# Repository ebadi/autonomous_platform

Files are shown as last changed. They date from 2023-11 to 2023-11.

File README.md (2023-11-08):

# Autonomous Platform (Gen4)

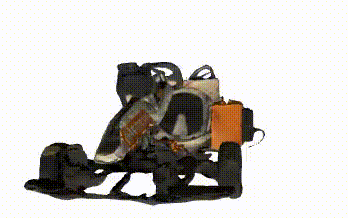
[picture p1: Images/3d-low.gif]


This is the repository for Autonomous Platform at Infotiv Technology Development. The new generation of Autonomous Platform was created by **Fredrik Juthe** and **Erik Magnusson** as part of a master thesis at Chalmers University of technology spring 2023 under supervision of **Hamid Ebadi**. The master thesis designed the system E/E architecture and implemented a base on which future functionality could be added to. A published version of the thesis with the title of **"Design of a modular centralized E/E and software architecture for a small-scale automotive platform"** is accessible in [in this link PDF ](Master_Thesis2023.pdf).

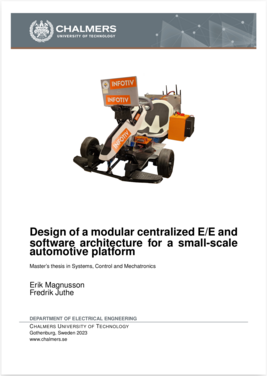
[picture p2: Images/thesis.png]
Design of a modular centralized E/E and software architecture for a small-scale automotive platform


INFOTIV logo (https://www.infotiv.se)
Chalmers logo (https://www.chalmers.se)

- The __latest public__ version of documentation and source code for Autonomous Platform (AP) project is available in the following address: [https://infotiv-research.github.io](https://infotiv-research.github.io) and [https://github.com/infotiv-research](https://github.com/infotiv-research).
- The printer friendly version of this document is [available in this link PDF](AutonomousPlatform.pdf).

## Introduction

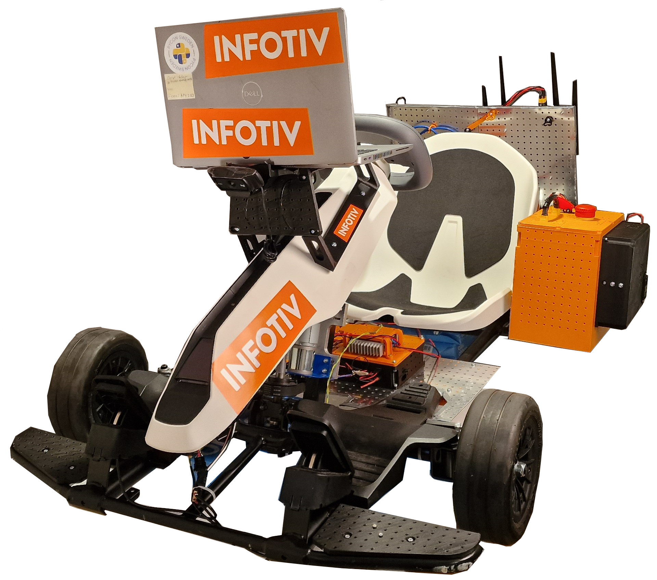
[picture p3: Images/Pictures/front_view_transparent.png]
Front view of platform after Master's thesis spring 2023


Autonomous Platform (generation 4) project is a platform on which internal and external research projects can be tested on. (i.e Autonomous Drive algorithms) and to expand the knowledgeable in different aspects of software and hardware system development. The purpose of this repository is to collect all the software components in one mono-repository, meaning all software (& hardware design) for the different components is placed in a single repository. Any future work on autonomous platform should be integrated into one of the repositories sub directories. This means that any future development or research can always refer back to previous work, making it a viable long term project at Infotiv AB.

## Features and Capabilities 

Below, the capabilities and functions of autonomous platform generation 4 are summarized.

### Drive by wireless controller

AP4 is capable to be remotely controlled using an xbox 360 controller.  The xbox wireless adapter should be connected to the Raspberry Pi 4b usb port.

### Remote access to platform & software

A wifi router is mounted on the back plate, this allows developers to connect to the software whilst it is running to monitor internal states. High-level software can stream commands to the low-level software remotely.

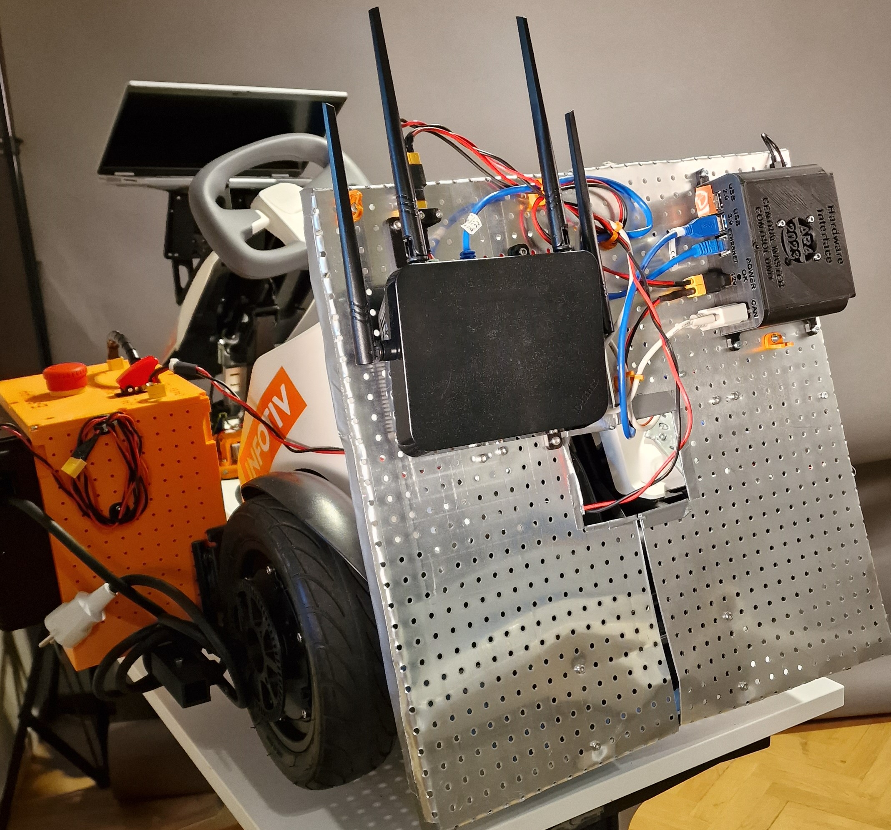
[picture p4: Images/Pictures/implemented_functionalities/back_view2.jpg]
View of the backplate where the wifi router and Raspberry Pi is mounted


### Accelerating, Brake & Steering

The platform can be driven forwards, backwards and can be steered. This is done programmatically, meaning "Drive by Wire". Joysticks commands from the xbox controller can therefore be configured to control the platform. In the same way it is trivial to take commands from Autonomous Drive algorithms to control the platform.

### Scalability

The idea with autonomous platform generation 4 is that it should be a scalable base platform on with future functionality should be added onto. Scalability and modularity is therefore a key concept for the platform. 

Hardware wise, every component can be mounted where it is deemed appropriate using a pre defined hole pattern. It is possible to move existing hardware as time goes on. New hardware can be added as long as it uses the pre defined hole pattern present on the metal sheets.

Embedded sensors can be added using ECUs following a set template. These can then be added to the existing system without breaking backwards compatibility using a defined CAN bus network. High data throughput sensors can be added to the platform using USB connection.

The software is built to be scalable and modular. The software structure is described in detail below. The software is deployed inside docker containers, making it easily deployable and scalable. The controlling software is written using the Robot Operating System 2 (ROS2) Framework. This allows developers to easily add onto existing software.

### Power Module

Consists of a led acid battery and a power supply unit, both can be connected to power the autonomous platform. Meaning the platform can be powered whilst driving around from battery. Whilst in a lab environment power can be supplied to the platform through a wall socket.

### Digital Twin 

The digital twin is implemented in the high-level software. It is described in detail in `High_Level_Control_Computer/README.md`. It is automatically started when the high-level docker container is started.

## System Architecture 

The autonomous platform has three different software components:

- High-level control
- Low-level control
- Embedded control

High-level is supposed to be run on a high performance computer and can be run without being connected to the rest of the system. Low-level control is run on the Raspberry Pi 4b mounted on the hardware platform. The embedded control is run on the ECU nodes mounted to the platform. Software in high-level and low-level are communicating using the Robot Operating System (ROS2) framework. Software in the embedded control is written using the Arduino framework.

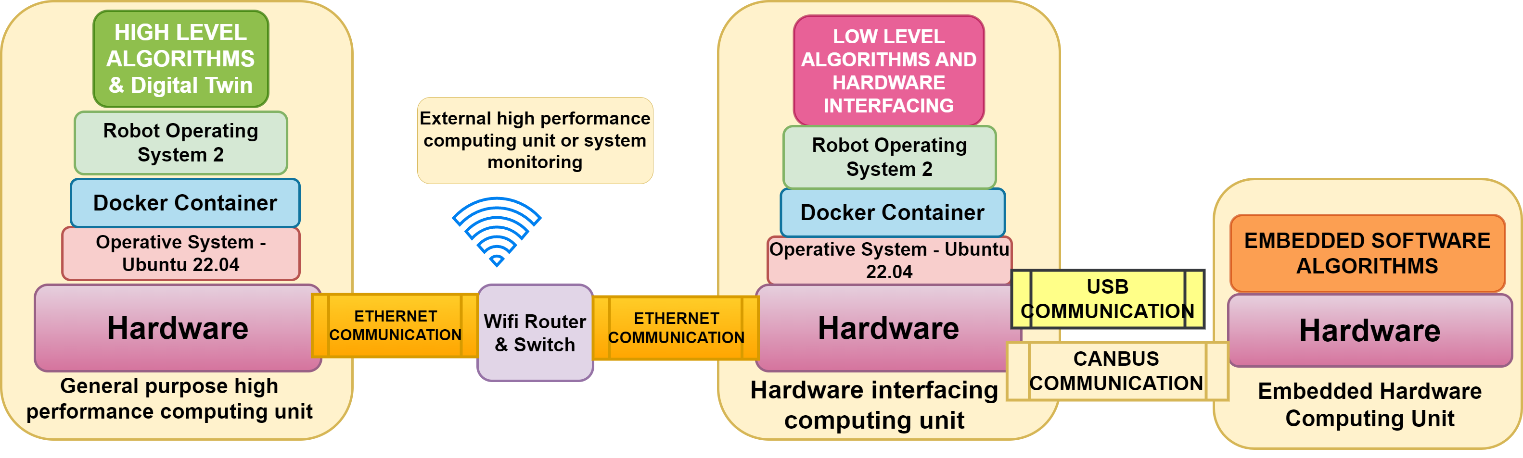
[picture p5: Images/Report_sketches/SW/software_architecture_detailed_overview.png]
System architecture and software layers illustrated
 

The three software components are connected through hardware and software links. High-level and low-level software is connected using an ethernet interface, meaning the two softwares should be run whilst connected to the same network. The low-level control is connected to the embedded control through a CAN bus network. A custom CAN library and interface has been created to link the embedded control with the low-level control.

###  High-level control

The high-level software consists of three components, an autonomous driving algorithm and a digital twin interface with the Gazebo physics simulator and a switch which sends commands to either the digital twin or the physical platform. As of June 2023 only a simple digital twin is implemented in this software layer. Starting up the high-level control container will start up Gazebo and Rviz. See `FUTURE_WORK.md` for what could be implemented.

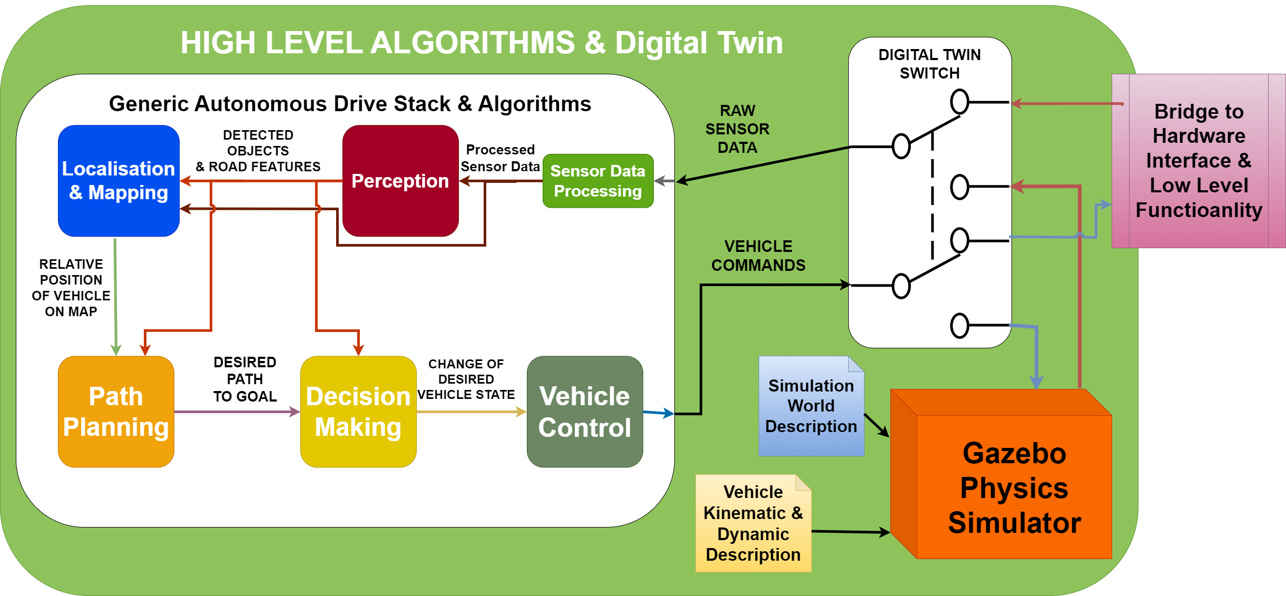
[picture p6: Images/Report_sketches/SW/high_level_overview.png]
high level overview
 
In the illustration above, three components can be seen. Autonomous driving stack, digital switch and gazebo physics simulator. These components should be implemented as a set of ROS2 computational nodes. Note: This is the intended structure but has not been implemented yet.

* __Autonomous Drving Stack__ is the proposed set of algorithms which takes in sensor information and responds with suitable actuator control commands. 
* __Digital Twin Switch__ is the proposed software switch that is supposed to re-route AD commands to either the physical platform or the digital twin. In the same way, sensory data should be routed from the physical platform or digital twin. The same actuator commands and sensor data type should be used on the digital twin as the physical platform. This ensures that proposed AD algorithms can first be tested on the digital twin and then seamlessly be tested on the physical platform.
* __Gazebo Physics Simulator__ Is the proposed digital twin simulation environment. It integrates seamlessly with the ROS2 framework. The physical dimensions and driving dynamics can be configured in xml format. Different simulation environments can be setup and saved as world files. Meaning different AD scenarios can be tested easily.

The high level control folder, `High_Level_Control_Computer` consist of a docker container and a folder with software. The software can start a simple digital twin of Autonomous platform Generation 4. The folder contains a `docker-compose` file which starts a docker container and mounts the `ap4_hlc_code` folder in the container. A ROS2 launch file is then run which starts up the digital twin. The container can be started on any device supporting graphics, i.e a laptop. 

###  Low-level control

The low-level software is responsible for taking platform commands sent from higher-level software and convert it into commands which are sent to the actuators. It is implemented on a Raspberry Pi 4b. A simple vehicle control converts commands sent on `\cmd_vel` ROS2 topic into ROS2 topics which gets relayed to the embedded control. In the same way the low-level software is responsible for taking any sensor input and passing it forwards to higher-level software. A custom package to convert ROS2 topics into CAN bus has been created, making it simple to interface high-level software with the embedded control software.

The hardware interface folder, `Hardware_Interface_Low_level_pc` , contains a `docker-compose` file which starts a docker container and mounts the `ap4_hwi_code` folder in the container. A ROS2 launch file is then run which starts up software that interfaces with hardware. This software is specific for the hardware mounted on autonomous platform, therefore it can only be started properly on the Raspberry Pi 4b mounted onto the platform.

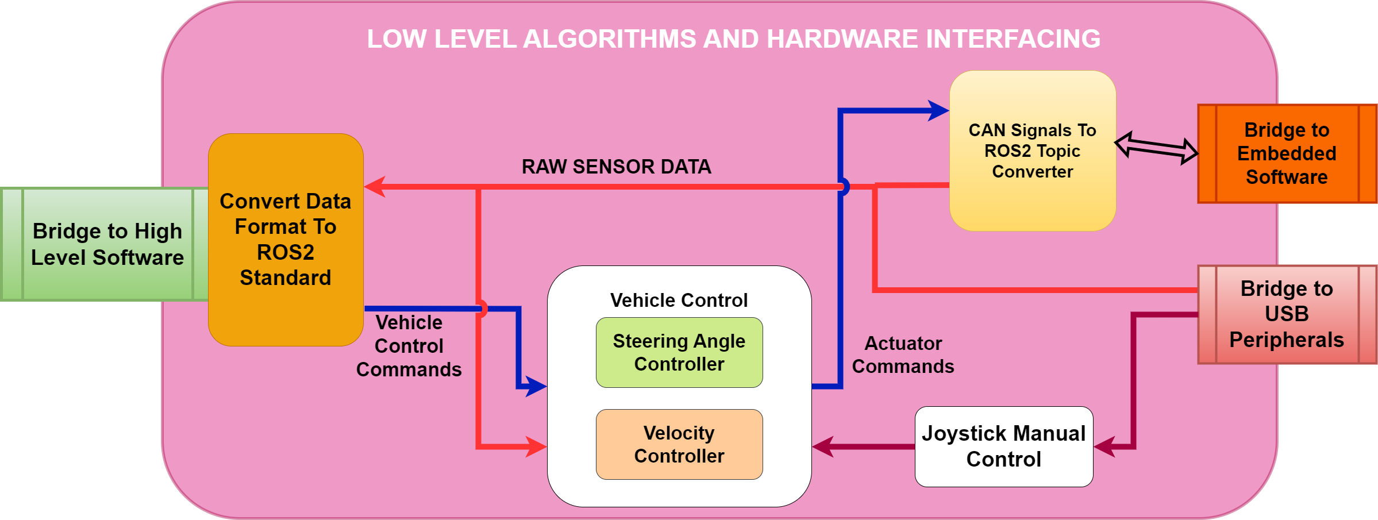
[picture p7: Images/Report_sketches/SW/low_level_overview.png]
low level overview
 

### Embedded control

The embedded software is implemented on the ECUs placed on the platform. This firmware acts as an interface between hardware (actuators or sensors) and pass data to and from the low-level software.
Currently a single embedded software is implemented, Steering and Propulsion Control Unit (SPCU).

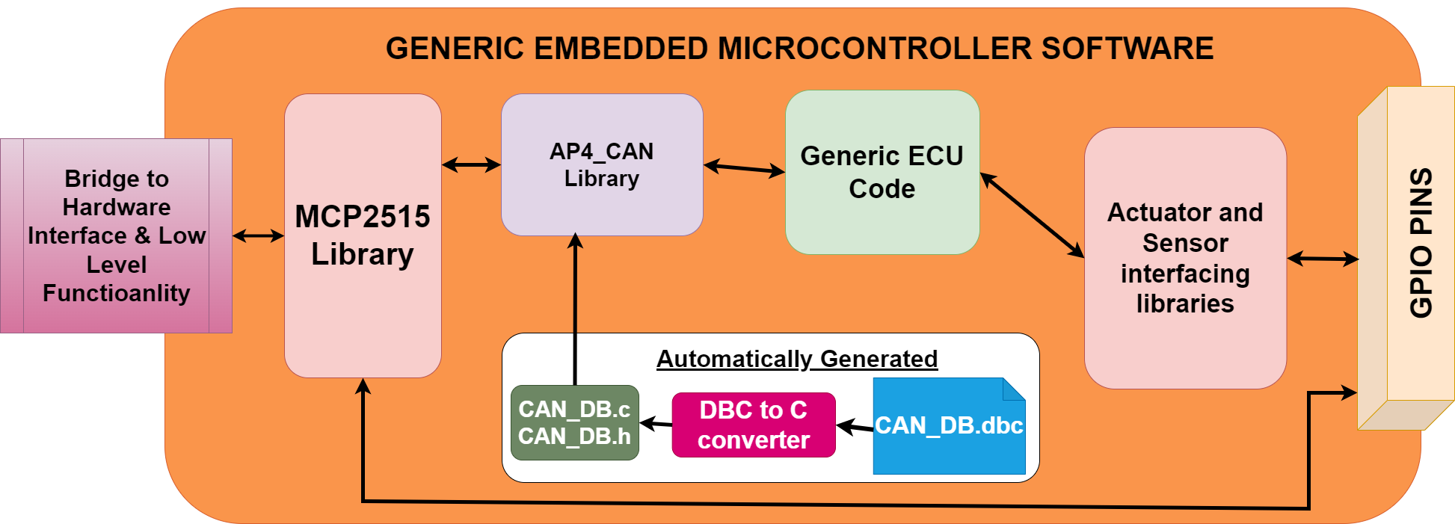
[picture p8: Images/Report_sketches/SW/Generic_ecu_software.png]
Embedded control
 

`CAN_Nodes_Microcontroller_Code` folder contain PlatformIO projects for each ECU, that is the embedded software running on the generic ECUs. An example of ECU is the SPCU (Steering, Propulsion Control Unit).Furthermore here is the CAN database and the corresponding CAN-library located.

## Start AP4 

Below follows a quick guide on how to start autonomous platform generation 4 and control it using an xbox 360 controller.

* Connect xbox wireless adapter to Raspberry Pi 4b
* Connect Power source: (Battery or PSU) to POWER IN plug. 
* Release Emergency stop
* Flip start switch
* Turn on Nine-bot segway (on backside of platform) Segway will beep once.

System will now boot up. The wheels will move back and forth.

* Wait 60 seconds (hardcoded in the SPCU ECU unit)

The platform should beep again after waiting 60 seconds and turn right to left, meaning it is ready to use.

The platform should be controllable using the xbox controller. By holding down the X button and moving the left joystick the front wheels should move and back wheels turn forwards.

## Connect (wireless) and start AP software stack

To check that the software is up and running as expected one can connect to the platform wirelessly and monitor the ROS2 network. On an external computer (dev-laptop or other linux computer) start the high-level software container. Make sure the computer is connected to the wifi network of autonomous platform. 

NOTE: User credentials are available only in the infotiv internal gitlab repository.

NOTE: high-level software automatically starts the digital twin simulation environment, the RVIZ and gazebo windows can be ignored.

In a new terminal, start the docker container:

```bash
cd High_Level_Control_Computer
docker-compose build
docker-compose up
```

In a new terminal, enter the docker container
```bash
docker exec -it ap4hlc bash
```

Source environment variables and export configuration environment variables
```bash
cd ap4hlc_ws
source install/setup.bash
export ROS_DOMAIN_ID=1
```

The low-level software components should be visible to the high level software components. This can be checked with
```bash
ros2 node list
```
The expected output will be something like this:

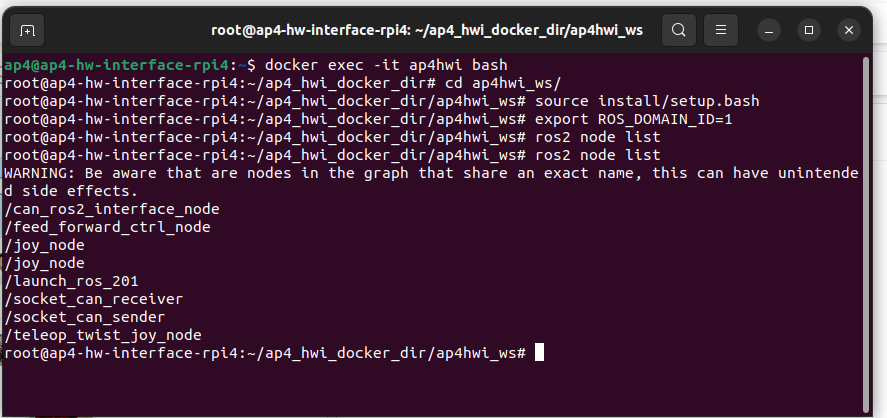
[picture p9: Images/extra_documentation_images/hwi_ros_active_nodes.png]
ROS active nodes


Information sent between nodes (such as sensor data or CAN bus traffic) can be monitored using
```bash
ros2 topic echo <topic_name>
```

For a list of active ROS2 topics, the following command can be used.

```bash
ros2 topic list
```

If the topics and nodes show up, the system has started correctly and can be controlled by either an xbox control or any future high-level software control. 

## Repository overview
The repository consists of three directories containing software (with a few subdirectories each):

 * [`CAN_Nodes_Microcontroller_Code`](CAN_Nodes_Microcontroller_Code/)
 * [`Hardware_Interface_Low_Level_Computer`](Hardware_Interface_Low_Level_Computer/) 
 * [`High_Level_Control_Computer`](High_Level_Control_Computer/) 

Within these directories, there exists useful documentation regarding each software component and sub components.

* `CAN_Nodes_Microcontroller_Code/README.md`
* `CAN_Nodes_Microcontroller_Code/CAN_LIBRARY_DATABASE/README.md`
* `Hardware_Interface_Low_Level_Computer/README.md` 
* `High_Level_Control_Computer/README.md`

The documentation is split up into smaller parts to keep information manageable and separated according to what can be relevant at a given time. The major documentation files located in the root directory of the repository are:

* [`README.md`](README.md) : The documentation you first see when you open the gitlab, this document. 
* [`SOFTWARE_DESIGN.md`](SOFTWARE_DESIGN.md) : A quick introduction to important software and frameworks used on AP4 and how to install the required software. In illustration of how the network of hardware is connected is also can be found there.
* [`HARDWARE_DESIGN.md`](HARDWARE_DESIGN.md) : An introduction to hardware that is used on AP4 and how to add a new one.
* [`HOW_TO_EXTEND.md`](HOW_TO_EXTEND.md) : Are you a new team member? Look at this file for a quick introduction to the project and how to get going. It also has a general design principles for the project to keep in mind when adding new functionality.
* [`TEST_DEBUGGING.md`](TEST_DEBUGGING.md) : Contains a list of known errors when working with AP4 and how to solve them
* [`ISSUES_AND_FUTURE_WORK.md`](ISSUES_AND_FUTURE_WORK.md) : A Comprehensive list of known bugs & issues and possible future work to be done on the platform.
* [`REQ_SPEC_BOOM.xlsx`](REQ_SPEC_BOOM.xlsx) contains a list of decided upon requirements and specifications which the autonomous platform should follow. A complete bill of materials (hardware components) can be found in this file. It contains items, what purpose they serve, where they can be bought and a total estimated cost.
As of *June 2023* the total cost is 16500 SEK to build the base platform and have spare parts over.

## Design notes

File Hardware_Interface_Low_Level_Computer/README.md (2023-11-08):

# Low-level Control & Hardware

## Introduction
This directory contains the software stack running on the Raspberry Pi 4b mounted to the hardware platform. It also aims to describe how each software component is designed / implemented.

In summary, the Low-level Control & Hardware Interface SW & HW is Hardware specific. It shall be run on the platform, connected to the embedded SW, CAN busses etc. It works as a bridge between high-level control software and the embedded ECU code which controls actuators / reads sensor data. 

Below an illustration of the low level and hardware interfacing software can be seen.

Low level overview

The software itself is implemented using the ROS2 framework, this software is then run inside a docker container. It is only meant to run on the Raspberry Pi 4b mounted onto autonomous platform and is very hardware specific. 

In the diagram above, four ROS2 packages are illustrated as rounded rectangles. These are;

## CAN Signals To ROS2 Topic Converter
This is a custom made ROS2 package made spring 2023. The purpose of it is to be a software translation of the CAN bus data from the embedded software layer to useful information available on ROS2 topics.

This abstracts the transfer of information between low level software and embedded software running on ECUs in the CAN network.

It uses the unified CAN bus database file (.dbc) for autonomous platform in order to decode the information sent on the CAN network. This database file is located at `autonomous_platform\CAN_Nodes_Microcontroller_Code\CAN_LIBRARY_DATABASE\CAN_DB.dbc`. A custom application is then written that maps a specific CAN signal onto a specific ROS2 topic. This means that every data signal sent over the CAN network can be used in algorithms located in the hardware interface and low level software. In the same way, ROS2 topics can be used to set the value of certain signals, meaning commands can be sent from the hardware interface and low level software to the various ECUs mounted onto autonomous platform.

### Vehicle Control
This is a custom made ROS2 package to control the steering angle and velocity of the hardware on a low level. It receives a desired velocity and steering angle on the `/cmd_vel` ROS2 topic and uses a controller gain to scale the values. The values have to be processed and rescaled in order for the embedded ECUs to actuate correctly. 

I.e to control the velocity, the embedded software in the SPCU expects a desired voltage to be sent on the CAN bus. Therefore the desired velocity needs to be converted into a desired voltage that should be applied on the accelerator pedal.

**More advanced control behavior can be implemented later on, I.e some sort of feedback from the velocity sensors. As of now it is open loop controlled**

### Joystick Manual Control
This is a set of ROS2 packages which enables a joystick to be connected to autonomous platform. The output will be in the form of a velocity commands on the `/cmd_vel` ROS2 topic. This output can then be read in vehicle control to control the gokart.

### Convert Data Format To ROS2 Standard
**This is not implemented yet for every data input**

The software layer connected to the hardware interfacing software layer expects input and output to be on specific ROS2 topics and uses standard ROS2 interfaces. I.e velocity commands to the platform will come to the hardware interfacing and low level software on the topic `/cmd_vel`, it is then up to this ROS2 package to convert it to a format which the lower level algorithms can use.

This can be as an abstraction layer.

The rectangular squares in the diagram above can be seen as input and outputs to the hardware interface and low level software layer. Higher level commands to the platform will come from the high level software. In the same way, this software layer will interface with the CAN network and USB peripherals for input and output. 

### Low-Level Control & Hardware Interface - Software / Hardware Requirements 

In terms of hardware, the low-level control software and hardware interfacing software is run on a Raspberry Pi 4b 4Gb. A RS485 CAN hat has been installed onto the GPIO pins. Power (5V,3A) is supplied from the platform using an LM2596 DC-DC converter to step down the platforms 12V power supply to 5V. A 32GB micro SD card is all the storage available. The hardware should be connected to the CAN network on Autonomous Platform Generation 4 (DB9 Connector) and to the wifi router/switch through an ethernet cable.

* [Raspberry Pi 4b Specifications](https://www.raspberrypi.com/products/raspberry-pi-4-model-b/specifications/)
* [RS485 CAN HAT Specifications](https://www.waveshare.com/w/upload/2/29/RS485-CAN-HAT-user-manuakl-en.pdf)
* [LM2596 Specifications](https://www.ti.com/lit/ds/symlink/lm2596.pdf)

Software wise, it uses a base installation of Ubuntu 22.04. A detailed guide on how to setup the software on a new fresh Raspberry Pi 4b can be found [here](#Installing-Base-Software-on-Fresh-Raspberry-Pi-4b).

When developing code for the low-level software it is possible to open the low-level software docker container on any linux based computer. It can be useful to have access to a proper IDE and not have to write code in notepad. Note: the CAN bus interfacing libraries will throw errors due to not being connected hardware wise. But once software compiles changes can be pushed and then pulled to the raspberry pi 4b.

### USB Devices Connected
There exists a USB hub mounted to the autonomous platform. This is connected to the Raspberry Pi 4b.

The following devices are connected
* Wireless keyboard and mouse
* Xbox Wireless Adapter

**Currently the USB hub is not mounted**

### Interfacing With Embedded ECUs 
The hardware interface and low level software can communicate with the embedded ECUs. Physically this is done through a Controller Area Network (CAN) bus with a D-Sub 9 connector. Software wise, a custom solution has been implemented for autonomous platform. The data sent over the CAN bus needs to be available on ROS2 topics in order for ROS2 nodes to be able to use the data in computations. In the same way, actuator commands sent from ROS2 nodes on ROS2 topics need to be sent to the ECUs over CAN.

The CAN frames sent over the CAN network must be encoded and decoded correctly and in the same way on both the hardware interface and embedded ECUs. Therefore a unified CAN database file has been constructed for autonomous platform . A helper library is used to convert the CAN database file into a set of C-style data structures.

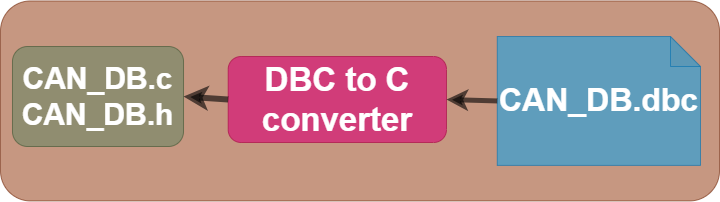
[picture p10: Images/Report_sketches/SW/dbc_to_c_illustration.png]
CAN communication information transportation illustration.
 

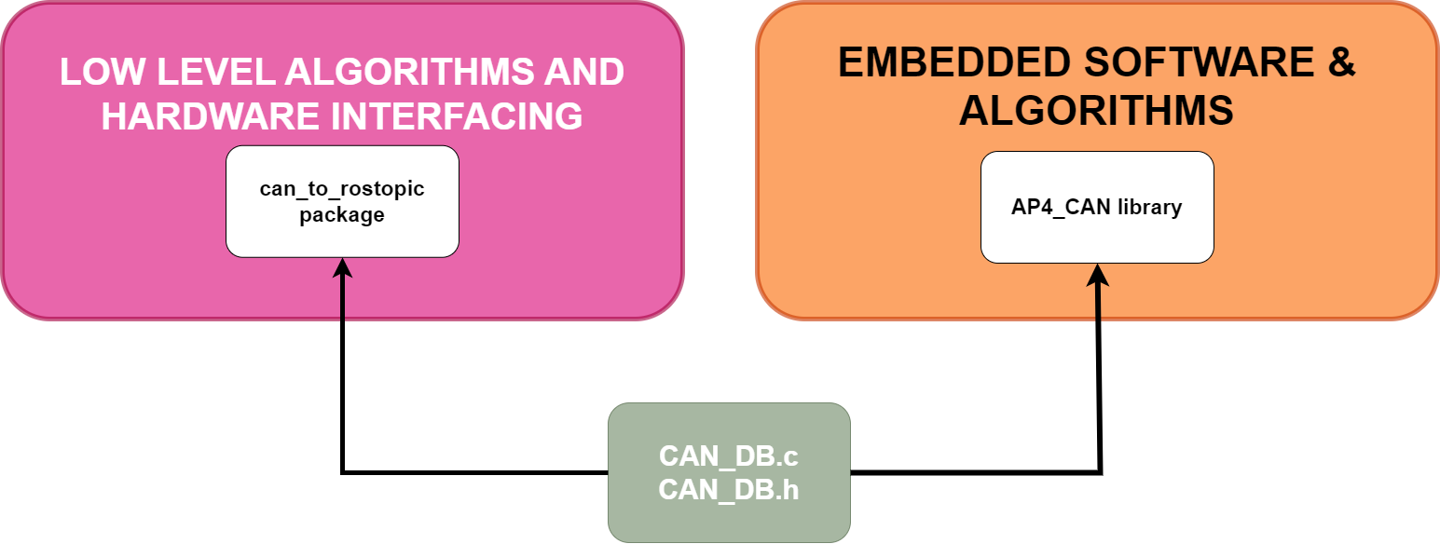
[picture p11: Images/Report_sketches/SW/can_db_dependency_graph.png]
 

Two custom made libraries have then been implemented, one in the embedded software and one in ROS2 in hardware interface and low level software.

How to extend this functionality with new CAN frames and signals is explained in detail in `Hardware_Interface_Low_Level_Computer\HOW_TO_EXTEND.md`. (The parts that are relevant to change in hardware interface and low level software is documented here). How to extended the software for the embedded ECUs is described in `CAN_Nodes_Microcontroller_Code\HOW_TO_EXTEND.md`.

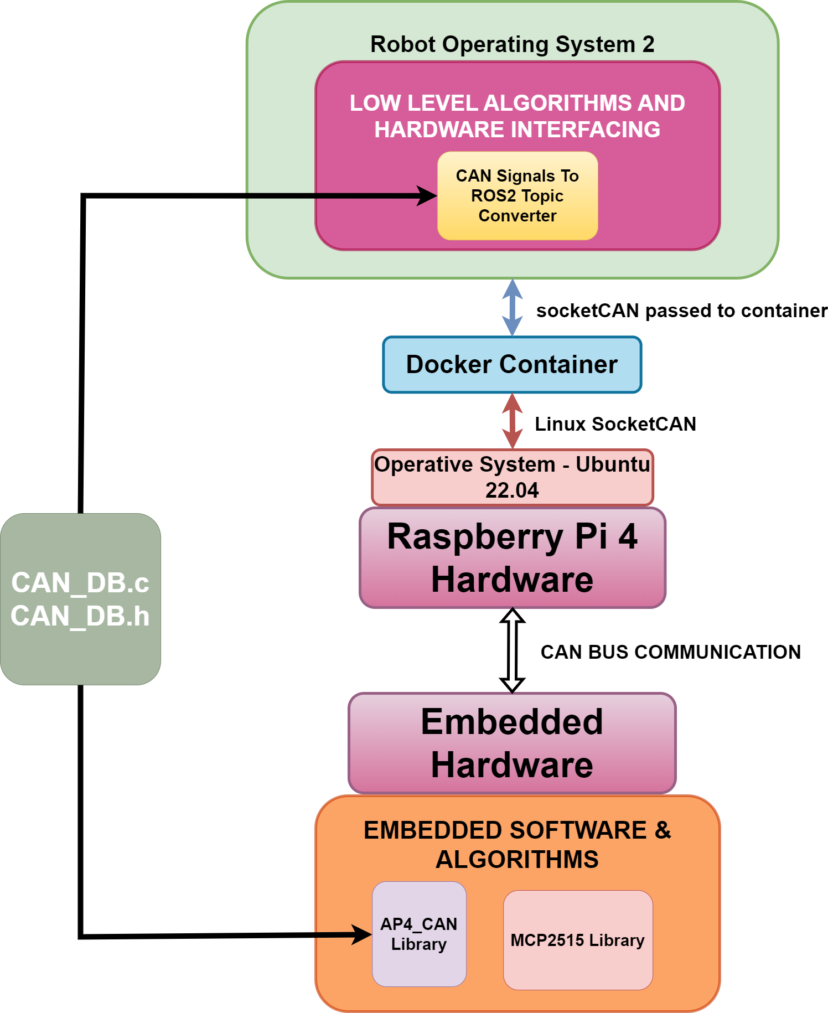
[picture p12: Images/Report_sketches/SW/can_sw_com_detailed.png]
 

### Interfacing with High Level Control Software 
The hardware interface and low level software can communicate with the high level control software running on an external computer. (I.e linux laptop- or intel NUC) This is done through an ethernet communication. A Wifi router is mounted to autonomous platform which means this can be done wirelessly.

Once an ethernet connection has been established, the two distinct ROS2 software networks (one on raspberry pi and one one on laptop) will be able to detect each other. This means that the two smaller ROS2 networks of nodes will become one large network with distributed computing power.

Network SSID and password is noted down in main `README.md` file of repository.

An important note, the ROS_DOMAIN_ID has to be configured to the value of 1 on both ROS2 networks.

### Adding New Functionalities 

How to add new functionality to the hardware interfacing software and low level algorithms is explained in `Hardware_Interface_Low_Level_Computer\HOW_TO_EXTEND.md`. 

### Automatic Startup of Software 
Once the Raspberry Pi 4b boots up it will automatically start the hardware interfacing and low level algorithm software. This is done using linux services that run on boot-up which in turn call the script "testing.bash".

If you need to change what is done during boot-up, edit the `testing.bash` script.

If the software does not automatically start, see **Software container not started?** in  `TEST_DEBUGGING.md` located in this directory.

### Installing Base Software on Fresh Raspberry Pi 4b 
See section in `SETUP_OF_RASPBERRY_PI.md`

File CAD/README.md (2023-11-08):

# CAD Appendix

<!---  AUTOMATICALLY GENERATED FILE. DONT EDIT THIS FILE DIRECTLY. EDIT thumbnail.sh INSTEAD --> 
STL files can be opened using any 3D printer slicer software, at Infotiv we use 'Ideamaker'. [Download here](https://www.raise3d.com/ideamaker/). Use a slicer configuration for an 'Raise3d E2' 3d printer. PLA material choice is fine if you don't leave autonomous platform in a hot car during the day. A base slicer profile for the Raise3D E2 can be found in the CAD profile. It is a nice starting point.

./Limitswitch_steering_holder/limittswitch_bottom_holder.stl:

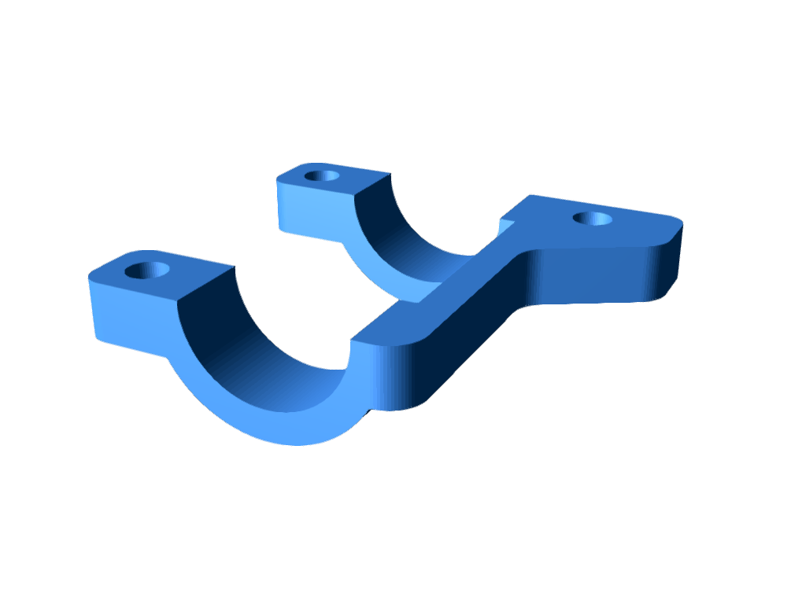
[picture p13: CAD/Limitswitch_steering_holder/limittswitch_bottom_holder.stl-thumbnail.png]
./Limitswitch_steering_holder/limittswitch_bottom_holder.stl


./Limitswitch_steering_holder/limitswitch_holder_top.stl:

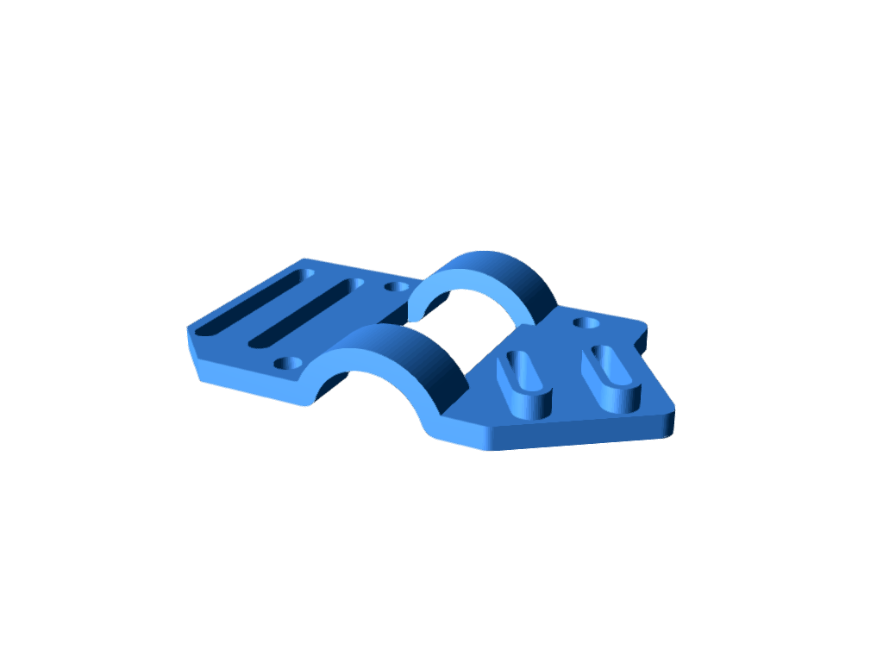
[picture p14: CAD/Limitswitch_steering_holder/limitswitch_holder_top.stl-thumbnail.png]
./Limitswitch_steering_holder/limitswitch_holder_top.stl


./Limitswitch_steering_holder/sensor_holder.stl:

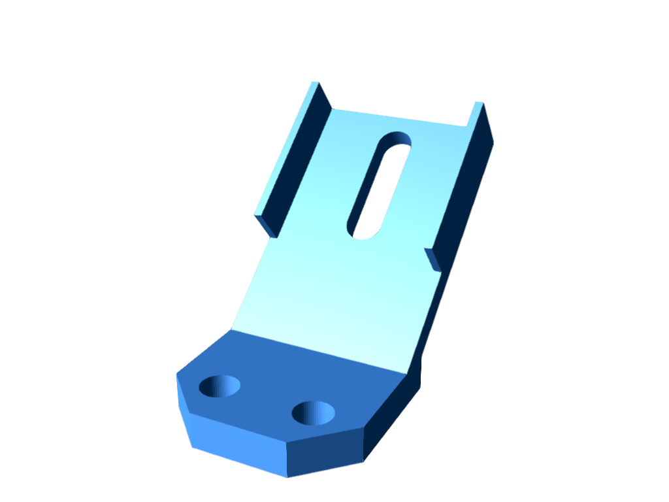
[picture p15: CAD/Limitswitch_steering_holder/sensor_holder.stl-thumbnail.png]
./Limitswitch_steering_holder/sensor_holder.stl


./camera_sensor_mount/camera_holder.stl:

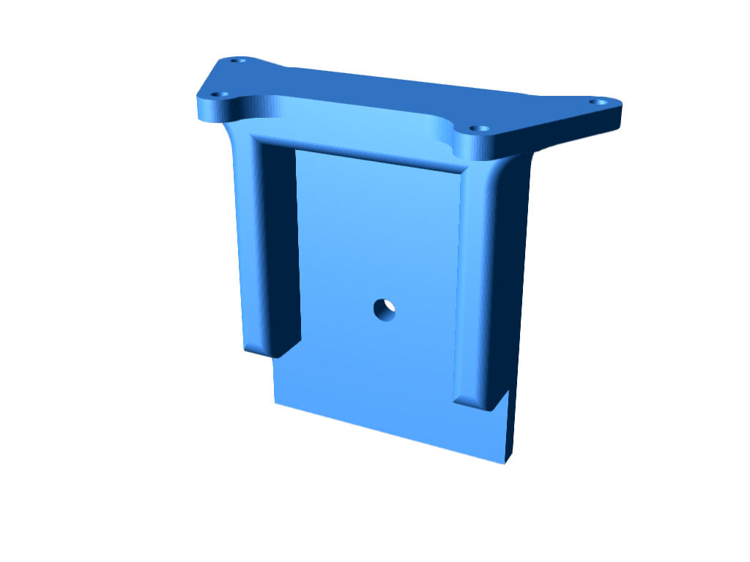
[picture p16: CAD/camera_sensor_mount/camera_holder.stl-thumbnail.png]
./camera_sensor_mount/camera_holder.stl


./Speed_Sensor_Back/Holder_base.stl:

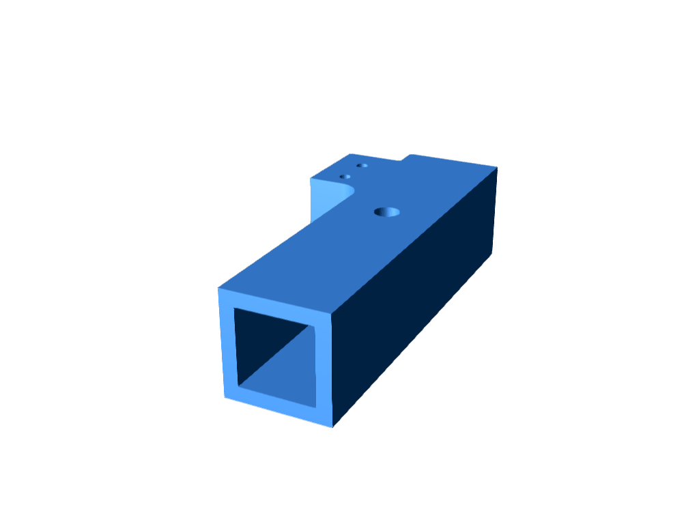
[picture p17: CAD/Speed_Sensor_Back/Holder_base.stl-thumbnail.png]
./Speed_Sensor_Back/Holder_base.stl


./Speed_Sensor_Back/Sensor_Holder.stl:

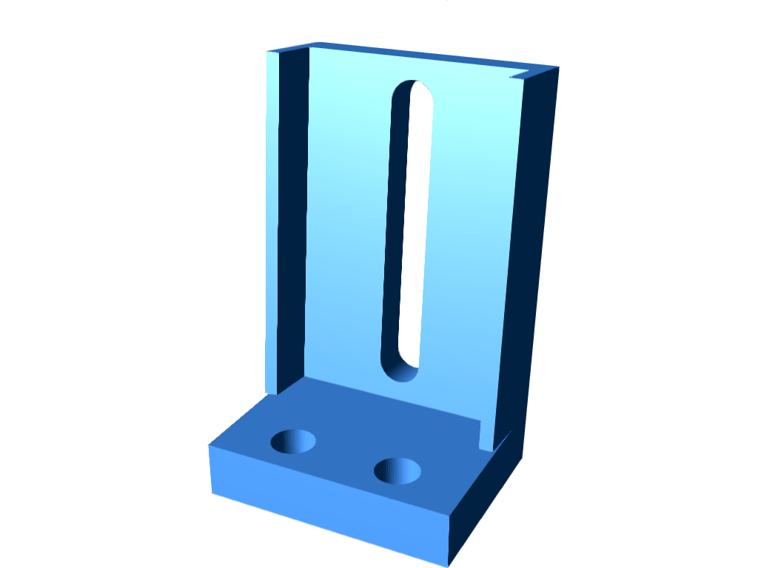
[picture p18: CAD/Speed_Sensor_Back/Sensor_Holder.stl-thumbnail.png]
./Speed_Sensor_Back/Sensor_Holder.stl


./Speed_Sensor_Back/Holder_ajustable.stl:

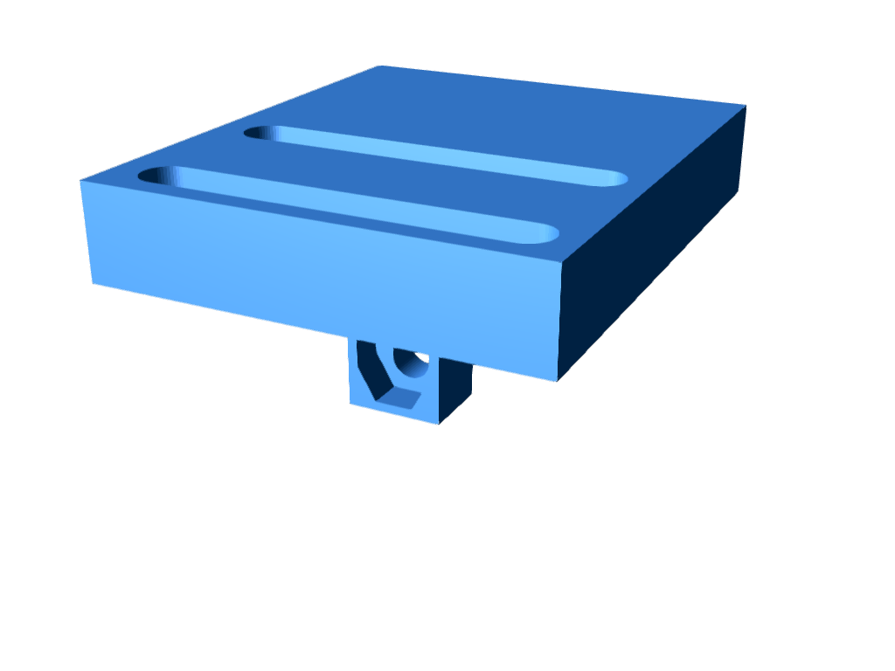
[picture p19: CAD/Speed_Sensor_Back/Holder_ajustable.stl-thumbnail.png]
./Speed_Sensor_Back/Holder_ajustable.stl


./Battery_BOX/x60_clamp.stl:

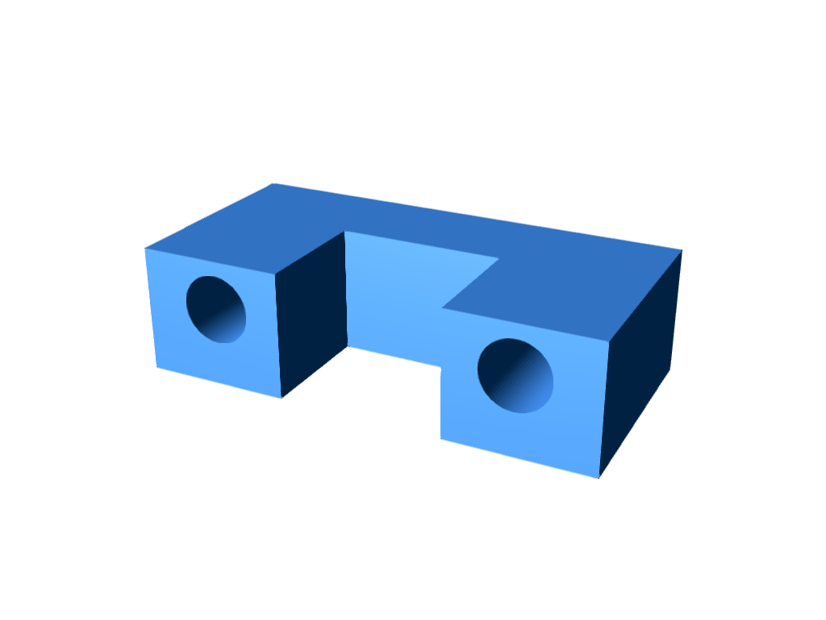
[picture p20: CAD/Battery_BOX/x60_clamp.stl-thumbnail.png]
./Battery_BOX/x60_clamp.stl


./Battery_BOX/Holder.stl:

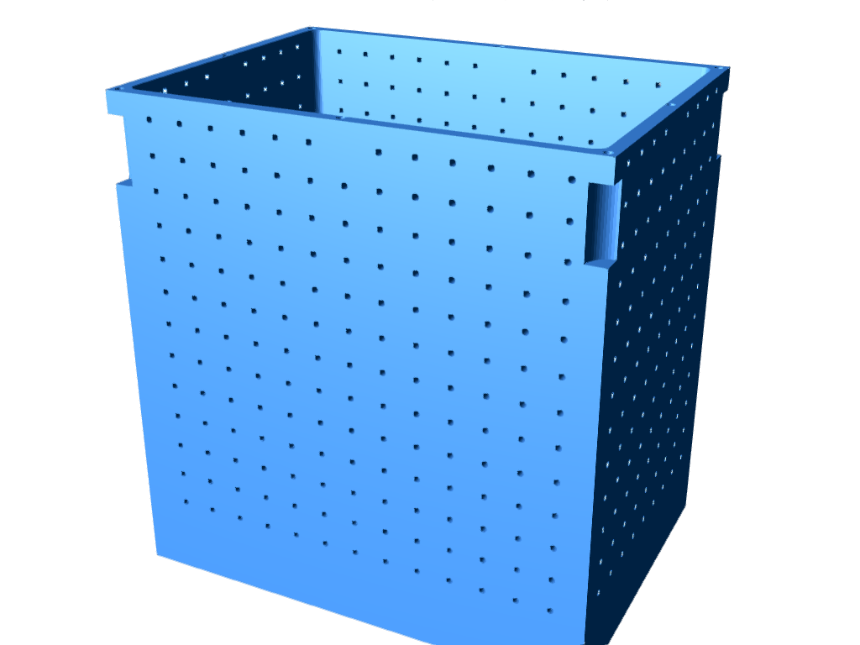
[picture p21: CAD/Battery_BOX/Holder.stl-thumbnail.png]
./Battery_BOX/Holder.stl


./Battery_BOX/Top.stl:

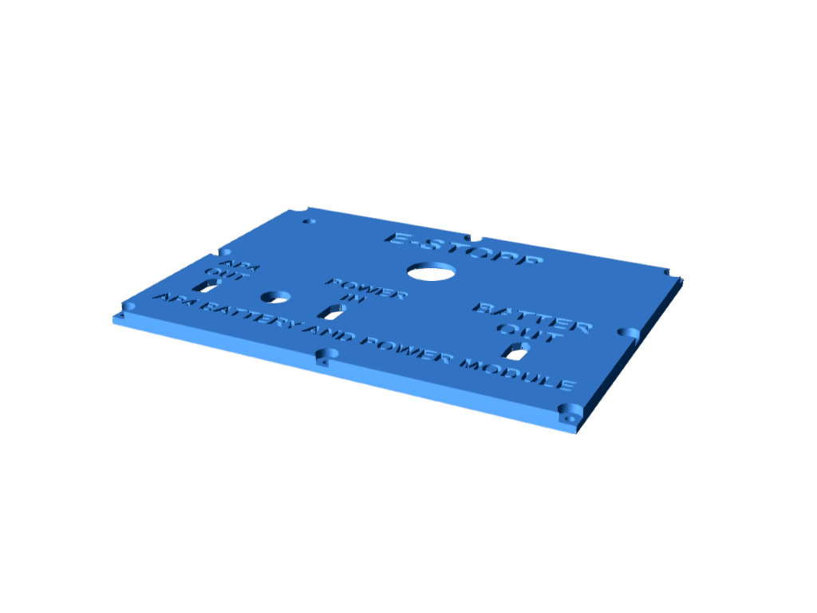
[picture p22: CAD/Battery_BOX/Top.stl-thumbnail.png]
./Battery_BOX/Top.stl


./Battery_BOX/Battery_charger_holder.stl:

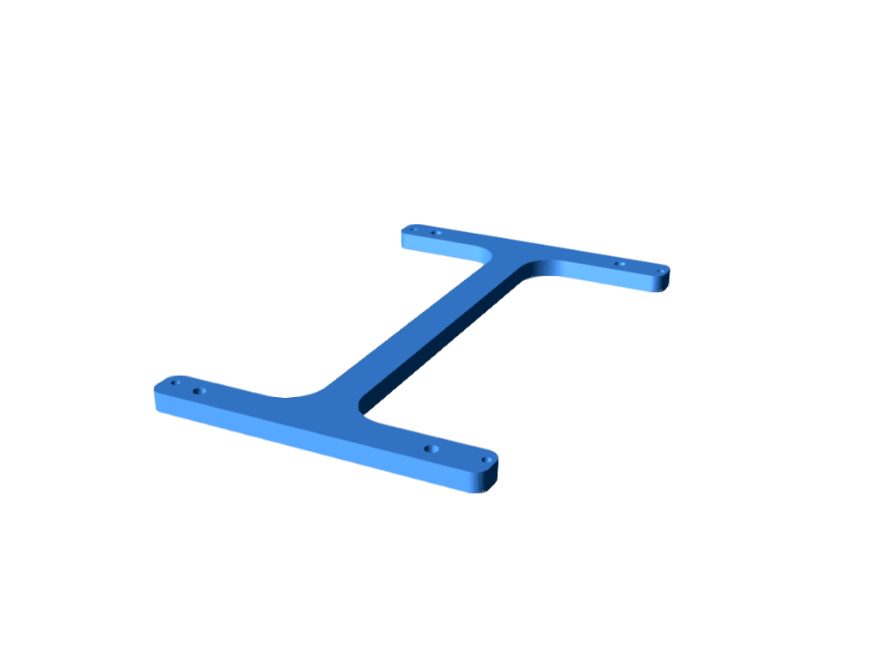
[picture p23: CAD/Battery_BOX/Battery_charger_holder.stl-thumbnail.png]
./Battery_BOX/Battery_charger_holder.stl


./Battery_BOX/din_rail_psu_holder.stl:

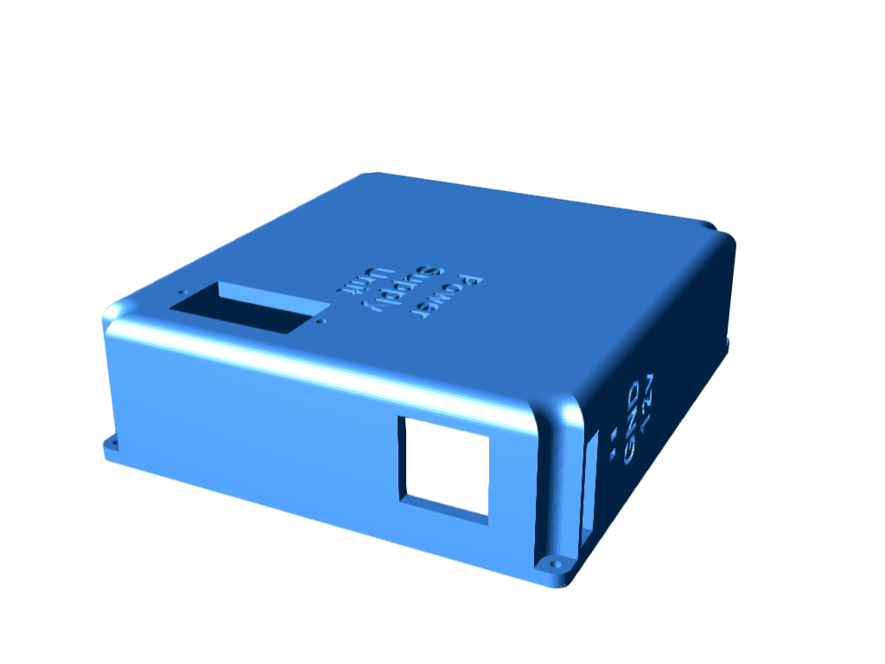
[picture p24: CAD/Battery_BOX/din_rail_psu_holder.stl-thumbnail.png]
./Battery_BOX/din_rail_psu_holder.stl


./Node_Box/Termination_Resistor_Bottom.stl:

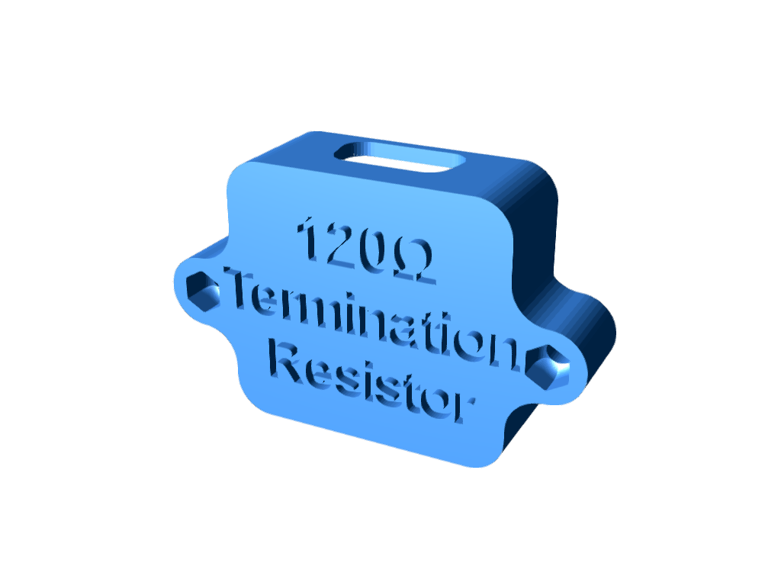
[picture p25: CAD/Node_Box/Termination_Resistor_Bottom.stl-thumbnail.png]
./Node_Box/Termination_Resistor_Bottom.stl


./Node_Box/cable_out_clamp.stl:

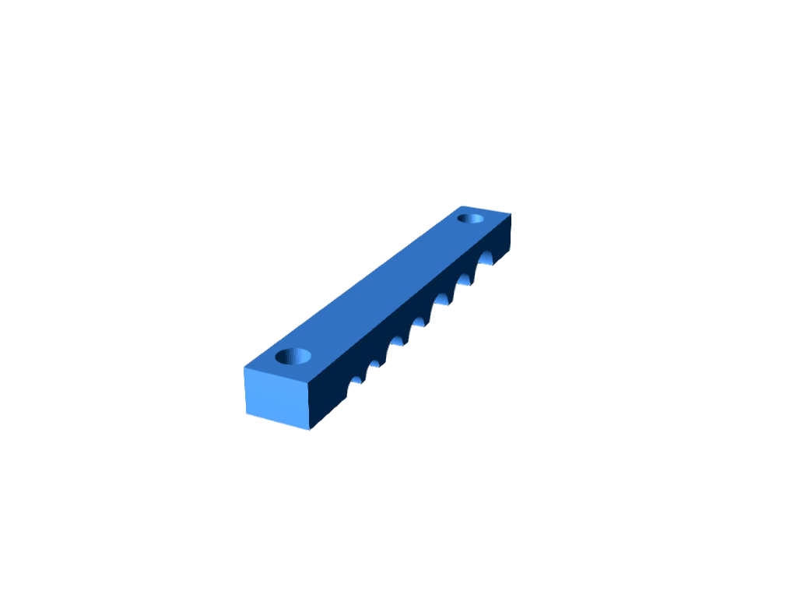
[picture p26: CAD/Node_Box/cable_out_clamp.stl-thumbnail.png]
./Node_Box/cable_out_clamp.stl


./Node_Box/ecu_nametag.stl:

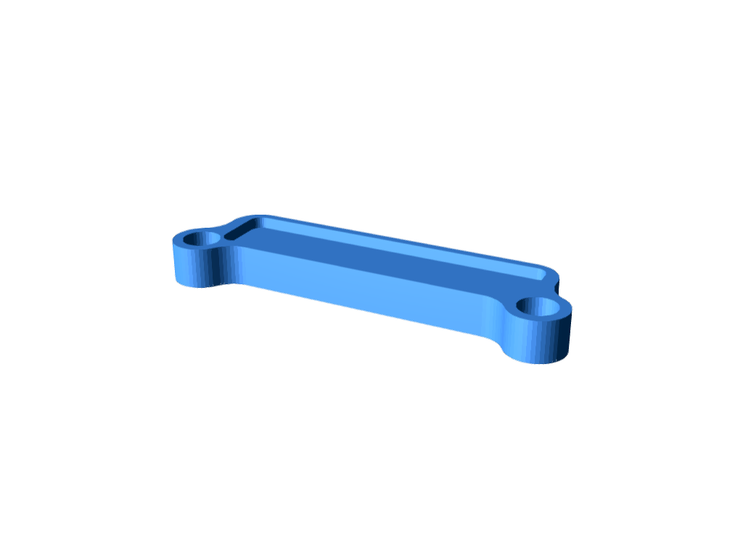
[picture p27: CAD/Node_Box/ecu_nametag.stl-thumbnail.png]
./Node_Box/ecu_nametag.stl


./Node_Box/xt60_clampdown.stl:

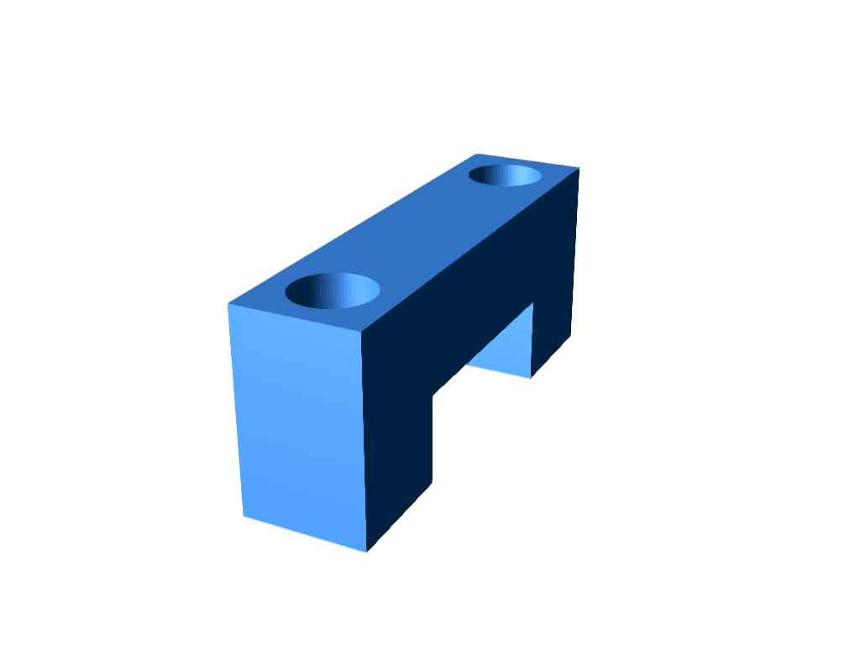
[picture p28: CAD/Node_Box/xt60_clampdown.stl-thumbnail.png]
./Node_Box/xt60_clampdown.stl


./Node_Box/HW_Node_Bottom_Box.stl:

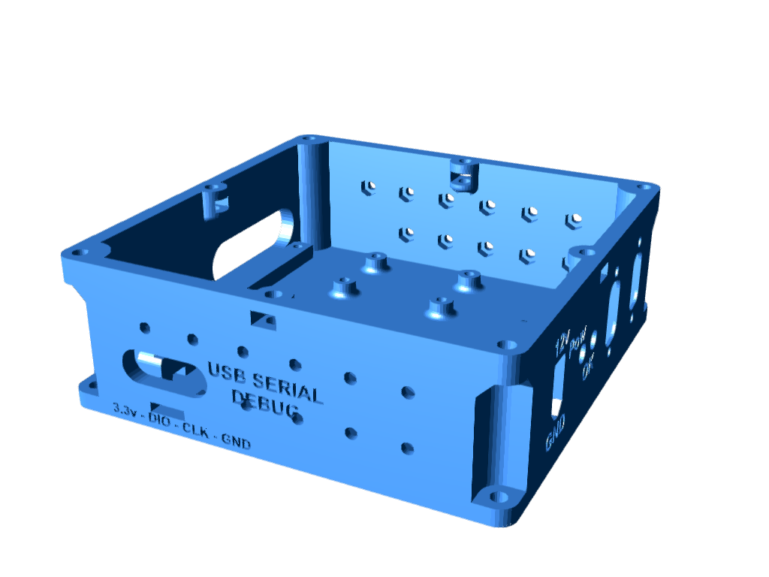
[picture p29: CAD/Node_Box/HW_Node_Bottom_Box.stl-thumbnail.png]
./Node_Box/HW_Node_Bottom_Box.stl


./Node_Box/Termination_Resistor_Bottom_Top.stl:

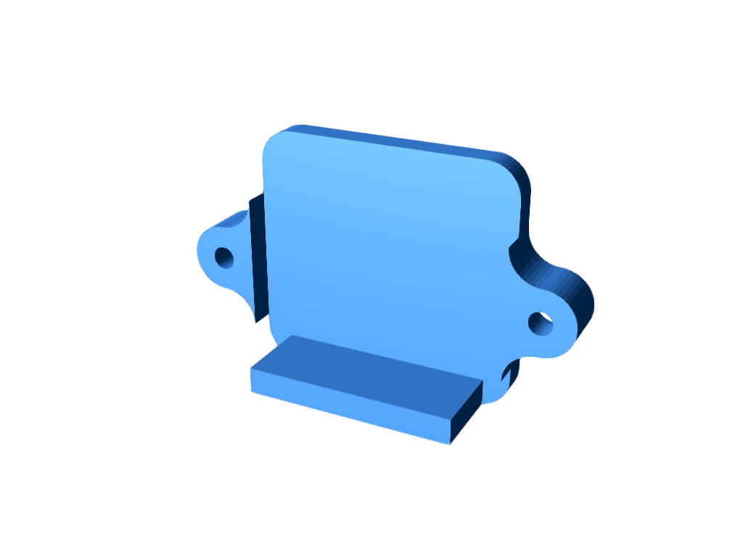
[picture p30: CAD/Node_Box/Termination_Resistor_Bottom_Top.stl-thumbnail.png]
./Node_Box/Termination_Resistor_Bottom_Top.stl


./Node_Box/HW_Node_Top_Cover.stl:

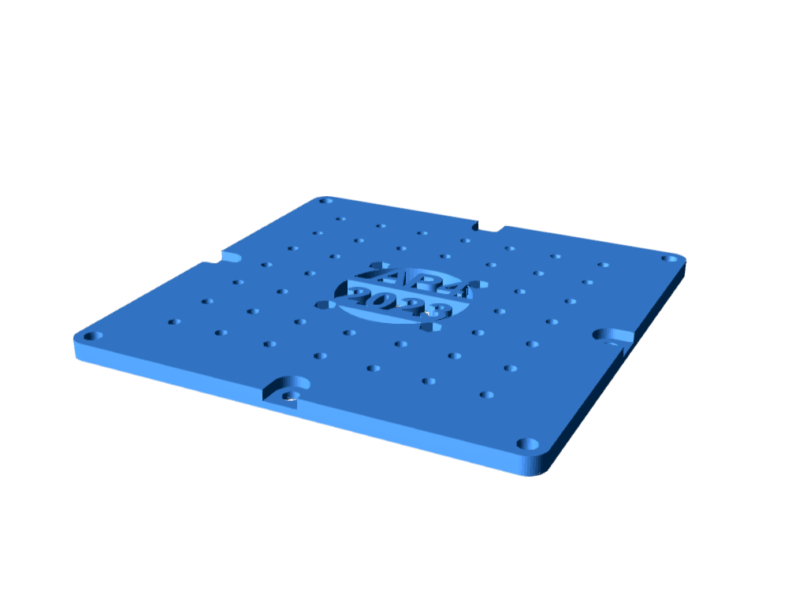
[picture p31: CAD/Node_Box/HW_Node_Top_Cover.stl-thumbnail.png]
./Node_Box/HW_Node_Top_Cover.stl


./Node_Box/STM32_bluepill_holddown.stl:

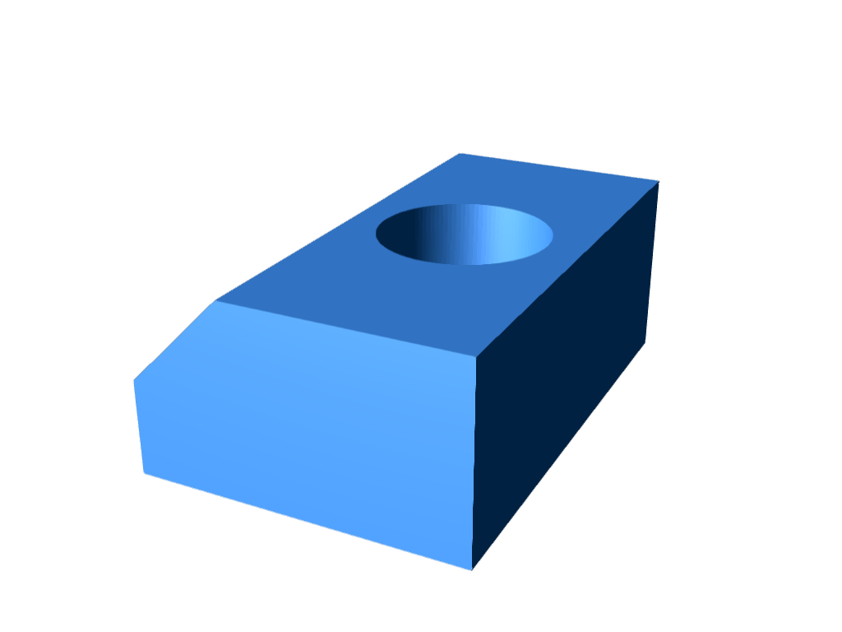
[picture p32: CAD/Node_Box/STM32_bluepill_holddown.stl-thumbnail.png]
./Node_Box/STM32_bluepill_holddown.stl


./Cable_Management/small_spiral_sleve_holder.stl:

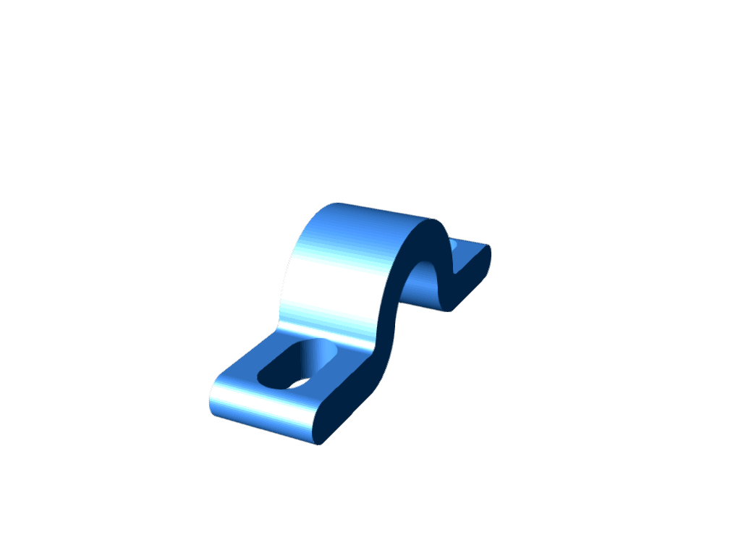
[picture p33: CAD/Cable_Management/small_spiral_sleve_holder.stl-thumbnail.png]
./Cable_Management/small_spiral_sleve_holder.stl


./Cable_Management/Cable_management_v2.stl:

./Cable_Management/Cable_management_v2.stl

./Cable_Management/big_spiral_holder_1.stl:

./Cable_Management/big_spiral_holder_1.stl

./Cable_Management/files/Cable_management2.0_2.stl:

./Cable_Management/files/Cable_management2.0_2.stl

./Cable_Management/files/Cable_management2.0.stl:

./Cable_Management/files/Cable_management2.0.stl

./Cable_Management/files/Cable_management2.0-4.stl:

./Cable_Management/files/Cable_management2.0-4.stl

./Cable_Management/files/Cable_management2.0-4.2.stl:

./Cable_Management/files/Cable_management2.0-4.2.stl

./Cable_Management/files/Cable_management2.0-3.stl:

./Cable_Management/files/Cable_management2.0-3.stl

./laptop_holder/laptop_left_holder.stl:

./laptop_holder/laptop_left_holder.stl

./laptop_holder/laptop_holder_hole_board.stl:

./laptop_holder/laptop_holder_hole_board.stl

./laptop_holder/laptop_right_holder.stl:

./laptop_holder/laptop_right_holder.stl

./Steering_Node_Box/sabertooth_holder.stl:

./Steering_Node_Box/sabertooth_holder.stl

./Steering_Node_Box/limittswitch_bottom_holder.stl:

./Steering_Node_Box/limittswitch_bottom_holder.stl

./Steering_Node_Box/limitswitch_holder_top.stl:

./Steering_Node_Box/limitswitch_holder_top.stl

./wifi_router_holder/xt60_holder.stl:

./wifi_router_holder/xt60_holder.stl

./wifi_router_holder/left_holder.stl:

./wifi_router_holder/left_holder.stl

./wifi_router_holder/right_holder.stl:

./wifi_router_holder/right_holder.stl

./Speed_sensor_holder/hole_wheel_speed_sensor.stl:

./Speed_sensor_holder/hole_wheel_speed_sensor.stl

./Speed_sensor_holder/front_holder.stl:

./Speed_sensor_holder/front_holder.stl

./Speed_sensor_holder/front_sensor_holder_lmitswitch.stl:

./Speed_sensor_holder/front_sensor_holder_lmitswitch.stl

./Speed_sensor_holder/front_speed_sensor_disc.stl:

./Speed_sensor_holder/front_speed_sensor_disc.stl

./front_win_grid/front_wing_grid.stl:

./front_win_grid/front_wing_grid.stl

./USB_Hub_clampdown/power_connection_holddown.stl:

./USB_Hub_clampdown/power_connection_holddown.stl

./USB_Hub_clampdown/hub_clampdown_bottom.stl:

./USB_Hub_clampdown/hub_clampdown_bottom.stl

./USB_Hub_clampdown/hub_clampdown_power.stl:

./USB_Hub_clampdown/hub_clampdown_power.stl

./USB_Hub_clampdown/hub_clampdown_top.stl:

./USB_Hub_clampdown/hub_clampdown_top.stl

./Back_plate_holder/holder_under.stl:

./Back_plate_holder/holder_under.stl

./Back_plate_holder/holder_top.stl:

./Back_plate_holder/holder_top.stl

./portable_screen_holder/Screen_holder.stl:

./portable_screen_holder/Screen_holder.stl

./Arduino_Mega_holder/bottom_nut_holder.stl:

./Arduino_Mega_holder/bottom_nut_holder.stl

./Arduino_Mega_holder/adapter.stl:

./Arduino_Mega_holder/adapter.stl

./Mounting_Plate/plate_holder.stl:

./Mounting_Plate/plate_holder.stl

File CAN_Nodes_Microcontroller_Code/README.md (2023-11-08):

# Embedded Software and Hardware (CAN nodes)

## Introduction
This document aims to describe how the embedded software layer is built in software and hardware, what purpose embedded software serves, highlight the design principles and how to extend functionality.

Keep in mind, this directory contains the software for several different ECUs mounted to autonomous platform generation 4.

### Prerequisites 
These are useful topics, skills and softwares to have some understanding of in order to work with the embedded software, hardware and CAN database

Recommended softwares to have installed:

* PlatformIO VSCode extension + ST-Link v3 Windows drivers
* KVASER CAN database editor
* Fusion360 (If you have to MODIFY existing CAD files)

Versions used when developing AP4 spring 2023:
- Visual Studio Code, version: 1.79.0 (user setup)
- Platform IO: version core: 6.1.7
- Kvaser Database Editor: version 2.4, [link to download](https://kvaser-database-editor.software.informer.com/2.4/)

### Introduction  
This directory contains several software components that is run in an embedded environment on ECUs mounted to the autonomous platform. There can be many different ECUs running at the same performing different tasks. All the code is contained in this directory in separate sub directories. This directory also contain the unified CAN database files which describes how data and information is sent between the different ECUs and the Hardware Interface Low Level software running on the Raspberry Pi 4b.

ECU functionality can be split up in several ways, for example by functionality. Software related to controlling the autonomous platform can be implemented on one ECU. Then on another ECU software for measuring speed can be run. It can also be split up by when certain functionality was added, instead of adding functionality to an existing ECU it can be easier, software wise, to create a new ECU with new software.

The new generation of Autonomous Platform is designed with the centralized Electrical / Electronic (E/E) architecture in mind. 

`HOW_TO_EXTEND.md`: The process of constructing a new generic ECU base from scratch

`HOW_TO_PROGRAM_A_BLUEPILL.md` : The flashing procedure (Upload New Software Into ECU)

### Centralized E/E Architecture Principles

The E/E Architecture of autonomous platform generation 4, developed during a thesis spring 2023 by Erik Magnusson and Fredrik Juthe. Currently (june 2023) only central master computer, CONCU and SPCU are implemented. 

A proposed system architecture can be seen below, where the "Central Master Computer" is consists of the Raspberry Pi 4b and development laptop. Every light blue rounded box would then be a separate ECU split by functionality. The specific ECU nodes are not set in stone and was more of a suggestion long term goal for future work during the spring 2023 thesis. What different ECUs are actually implemented are described further down below.



 [Paper on approaches to centralized hardware can be found here.](https://semiengineering.com/technical-and-structural-approaches-to-centralize-automotive-e-e-architectures/). The main points to keep in mind when developing software and hardware for a centralized E/E architecture are:

- No Heavy computations inside ECUs
    - Only serve as an INTERFACE with hardware
    - Minimal number of computations and instructions in each ECU to keep the run-time-cycle short and enable real-time capabilities
    - Main loop should not exceed 20ms in runtime
    - Read actuator commands from central master computer and actuate actuators
    - Read sensor data from hardware and send back to central master computer
    - Heavy computations are done in Central master computer and its High level algorithms
- Communication between ECUs and Hardware Interface and Low Level Software shall be done through CAN bus protocol
    - Due its robustness
    - Scalable
    - Standards, possible to use 3rd party softwares and tools to analyze behavior

### Embedded ECUs
This section describes the embedded ECUs present on autonomous platform generation and what function they serve. As of august 2023 there are two ECUs implemented.

### HW_Node_SPCU : Steering and Propulsion Control Unit 

Developed by Fredrik Juthe and Erik Magnusson spring 2023.

SPCU rendering

SPCU rendering

This ECU is responsible for actuating the propulsion and steering of autonomous platform generation 4. It also sends measurement of the current stearing angle back to the hardware interface low level software.

The code is located in `HW_Node_SPCU` folder.

Specific CAD and stl files for front and back speed sensors are located in `autonomous_platform\CAD\Speed_sensor_holder`.

More about this ECU, development processes and documentation can be found in `Propulsion_Steering.md`, `Shared_HW_Node_Libraries/SteeringMotorInterface/documentation_and_research/README.md` and 
`Shared_HW_Node_Libraries/PropulsionInterface/documentation_and_research/README.md` markdown file located in this directory.

#### Additional Components
Compared to a generic ECU on autonomous platform, the SPCU ECU has some extra components:

* Kangaroo x2 Controller + Sabertooth 2x50 DC motor driver
* MCP4725 DAC converter

The kangaroo x2 controller board is connected to the sabertooth 2x50A DC motor driver. It is a closed loop controller for the steering wheel motor. The kangaroo card can be controlled through a serial connection from the ECU. The current steering angle can be read from the kangaroo card. A custom library was created in order to control the steering angle.

To control the propulsion of autonomous platform generation 4, it was decided to send out analog voltages to the gokart pedals to spoof the pedals being pressed. (Throttle + Break). This is done by wiring a Digital to Analog Converter (DAC) to each pedal in parallel. The gokart has an internal controller black box mounted in the front nose, this will interpret the pedal presses and actuate the electric motor driving the platform forward. A brake pedal press will always override a accelerator pedal press due to how the black box works. This is a useful feature, when an operator is sitting on the gokart he or she can always stop the platform by applying the brakes.

### HW_Node_SSCU : Speed Sensor Control Unit
Developed by Seamus Taylor and Alexander Rydeval summer 2023.

SSCU rendering

This ECU is responsible for relaying the current velocity of the autonomous platform to the hardware interface and low level software. One speed sensor was mounted to the front right wheel on the hardware platform and it was showed that the velocity could be read from one wheel by measuring how fast the wheel turned. 

There exists CAD files for the remaining three speed sensors (one for every wheel).

The code is located in `HW_Node_SSCU` folder.

Specific CAD and stl files for front and back speed sensors are located in `autonomous_platform\CAD\Speed_sensor_holder`. 

More about this ECU can be found in `Speed_Sensor.md` markdown file located in this directory.

#### Additional Components
Compared to a generic ECU on autonomous platform, this ECU has some extra components:

* MCP4725 - Speed Sensor

### Generic ECU Hardware and Software
The first version of the generic ECU was developed by Fredrik Juthe and Erik Magnusson spring 2023.

Every ECU present on autonomous platform generation 4 shall be based on the same base hardware and software. Onto this base features specific to the function of a ECU can be added. By having a standardized base ECU it will be easier to understand how previous functionality was added, and it will be easier to add future functionality as much information can be transferred from previous ECUs.

A problem on autonomous platform generation __3__ was that is was unclear how previous functionality was implemented. There were more than three types of microcontroller used on the platform and every solution was custom made. As the people who implemented this left the project it was very unintuitive for new project members to understand how functionality was implemented. Many functions were hardcoded on unknown hardware.

As an improvement to this, on autonomous platform generation 4 the idea was therefore to standardize how embedded hardware and software implemented. If one chooses a suitable microcontroller with a lot of performance overhead, in theory any embedded sensor or actuator could be connected to it. The hardware for each embedded system could therefore use the same microcontroller. And to simplify things further, the most used components could be constructed as a finished hardware package. The software and connection for a specific function could be configured.

That was how autonomous platform generation 4 ended up with a **generic ECU base**. A hardware template on which to connect any sensor or actuator to a powerful microcontroller. Any future ECU should follow this standard of implementing functionality on top of a ECU base.

## Generic ECU Template
The generic ECU has predefined set of hardware. It was designed with future proofing in mind so that it could be used for future work as well.

A high level schematic of the components present in the generic ECU base can be seen below. For any new embedded functionality (Input or output), these components would be needed. Therefore it might as well be assembled into a module.

Schematic of generic ECU

A rendered illustration of the ECU can be seen below. The top cover is not illustrated.

Rendered 3d model of ECU

### Key Components of Generic ECU

* __Microcontroller__ : 
    The microcontroller was Chosen to be STM32F103C8T6, often referred to as an STM32 bluepill. It has plenty of I/O, a fast processor and there exists very much documentation and resources for this microcontroller. 
The official documentation can be found for the STM32F103C8T6, can be found [here](https://stm32-base.org/boards/STM32F103C8T6-Blue-Pill.html).

* __CAN Reciever and Controller__:
    The ECU needs to be connected to the Hardware Interface and Low Level Software through a CAN bus, therefore the generic ECU needs a CAN bus interface. The MCP2515 / TJA1050 board was choosen as it combines a CAN controller and a CAN tranciever on a single PCB. There exists many arduino libraries for this.
The datasheet for MCP2515 / TJA1050 can be found [here](https://www.electrokit.com/uploads/productfile/41017/MCP2515-Data-Sheet.pdf) and [here](https://www.electrokit.com/uploads/productfile/41017/TJA1050-Data-Sheet.pdf).

* __DC-DC Converters__ :
    The components inside the generic ECU needs to be powered using 3.3v and 5v. And any additional sensor or actuator may need to be powered as well. Therefore, the generic ECU base has two DC-DC voltage step down converters. The LM2596 DC-DC converter was deemed suitable. It can output a maximum of 3 A of current which is well above what any embedded sensor would use.
Datasheet for the LM2596 dc-dc converter can be found [here](http://tpelectronic.ir/datasheets/20150123144301750.pdf).

* __Inputs and Outputs__:
    The generic ECU node has a predefined set of Input and Outputs. This allows the connection between various ECUs and the Raspberry Pi 4b hardware interface and low level software to be standardized. The CAN communication on AP4 uses a D-Sub 9 pin connector. The generic ECUs can be chained together with D-Sub 9 pin cables to create a CAN bus network. In the same way the power distribution of autonomous platform generation 4 can be standardized, power is supplied to the generic ECU through an XT60 connector. This one can also be chained between nodes, providing 12v input to each generic ECU.

| **Component** 	| **Purpose** 	| **Documentation** 	|
|:---:	|:---:	|:---:	|
| STM32-F103C8T6 "Bluepill" 	| Programable processor and GPIO pins 	| [Datasheet](https://www.alldatasheet.com/datasheet-pdf/pdf/201596/STMICROELECTRONICS/STM32F103C8T6.html) 	|
| Logic converter 	| To step down voltage to SMT32-F103C8T6 logic levels (3.3 V). Important at the CAN module interfacing with bluepill 	| [Bought at](https://www.elfa.se/sv/dubbelriktad-omvandlare-av-logisk-spaenningsniva-sparkfun-electronics-bob-12009/p/30145425) 	|
| DC-DC converter 	| LM2596, possible to manually change voltage levels 	| [Datasheet](https://www.onsemi.com/pdf/datasheet/lm2596-d.pdf) 	|
| CAN controller and Transeciever 	| MCP2515, to interface with CAN network, decode and encodes messages 	| [Datasheet](https://ww1.microchip.com/downloads/en/DeviceDoc/MCP2515-Stand-Alone-CAN-Controller-with-SPI-20001801J.pdf) 	|
| PC Fan 	| Fan to cool each component in the ECU 	| [Bought at](https://www.elfa.se/sv/axialflaekt-dc-40x40x10mm-12v-13-9m-sunon-ee40101s1-1000u-999/p/30129654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) 	| 
|DB9 Male| Outlet for CAN bus communication| |
|XT60 Male| Outlet for power supply| |

### Software Template and Setup
In the same way as the hardware as been standardized, work has been done to standardize the software development and deployment on autonomous generation 4 embedded hardware.

The idea is that basic software needed for every generic ECU base should already be implemented and setup. A developer should not have to start from scratch and rewrite the basic interfaces has already been used on other generic ECU nodes.



An illustration of what software components are needed for every generic ECU can be seen above.

When developing a new ECU with new functionality, the developer only has to think about the green and purple code blocks, the main loop code and what libraries to add.

Therefore, a template ECU code directory has been created, `HW_NODE_CODE_TEMPLATE`, this is a PlatformIO project that have been configured with the correct path variables to find the custom CAN library or any other custom made library. Microcontroller and other configuration variables have been set in the `platformio.ini` file. To create software for any new future ECU one simply has to make a copy of this directory to get a basic software running on the ECU node. 

Just as the Arduino IDE, PlatformIO has a library for almost any sensor or actuator. You can search the project library [here](). To include an existing library into a PlatformIO project one simply has to include it under __lip deps__ tag in the platformio.ini file.

### Bill of Material for Generic ECU
The complete bill of materials for a generic ECU base can be found below.

| Component Name| Function |  Quantity | Datasheet/ Manual | Product Buy Link | Estimated price (SEK)|
| :-----: | :---: | :---: | :---: | :---: | :---: |
| STM32F103C8T6 "Bluepill" | Microcontroller - Runs embedded SW  | 1 | [Link](https://stm32-base.org/boards/STM32F103C8T6-Blue-Pill.html) | [Link](https://www.amazon.se/AZDelivery-mikrokontroller-STM32F103C8T6-utvecklingskortmodul-M3-processor/dp/B07TSKNWQQ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) | 100 
| MCP2515 | CAN controller / transceiver | 1 | [Link](https://ww1.microchip.com/downloads/en/DeviceDoc/MCP2515-Stand-Alone-CAN-Controller-with-SPI-20001801J.pdf) | [Link](https://www.amazon.se/ZkeeShop-CAN-bussmodul-mottagare-kompatibel-utvecklingskort/dp/B07SYH9BXS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) | 50
| Logic Level Converter | Converts MCP2515 5V signals to 3V which makes it compatible with STM32 Bluepill | 1 | [Link](https://www.elfa.se/Web/Downloads/_t/ds/BOB-12009_eng_tds.pdf) | [Link](https://www.elfa.se/sv/dubbelriktad-omvandlare-av-logisk-spaenningsniva-sparkfun-electronics-bob-12009/p/30145425) | 40
| LM2596S | Converts 12V to 5 & 3.3V | 2 | [Link](https://www.makershop.de/download/um_lm2596_d.pdf) | [Link](https://www.amazon.se/gp/product/B07DP3JX2X/ref=ppx_yo_dt_b_asin_title_o00_s00?ie=UTF8&psc=1) | 50
| DB9 Breakout Board | Exposes individual pins on DB9 Connector to Connect wires to | 2 | --- | [Link](https://www.amazon.se/SIENOC-RS232-D-SUB-terminalkontakt-signalmodul/dp/B01M8JRDN0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) | 130
| 40x40x10 mm 12V Fan | Cool Down Internal Components in ECU base | 1 | --- | [Link](https://www.elfa.se/sv/axialflaekt-dc-40x40x10mm-12v-13-9m-sunon-ee40101s1-1000u-999/p/30129654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) | 52
| Breadboard Jumper Wires Pack of 10| Wire Internal Components of ECU | 2 | --- | [Link](https://www.elfa.se/en/jumper-wire-female-to-female-pack-of-10-pieces-150-mm-multicoloured-rnd-components-rnd-255-00011/p/30115109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) | 20
| Biltema Mini Fuse Holder | Internal ECU Fuse holder | 1 | --- | [Link](https://www.biltema.se/bil---mc/elsystem/sakringar/sakringshallare-mini-2000016466) | 33
| Mini Fuse 3A | --- | 1 | --- | [Link](https://www.biltema.se/bil---mc/elsystem/flatstiftssakringar/flatstiftssakring-mini-10-st-2000016468) | 25
| XT60 Connector Male | Connect to AP4 12V Power System | 1 | --- | [Link](https://www.conrad.se/p/reely-1399717-batterikontakt-xt60-foergylld-20-st-1399717) | 21
| (Optional) XT60 Y Splitter | Splits one XT60 Connecting in Y configuration | 1 | --- | [Link](https://www.conrad.se/p/adapterkontakt-2x-xt60-1x-xt60-parallellt-ansluten-reely-1373227) | 70
| Green LED | @Future work Indicate System Status of ECU | 1 | --- | [Link](https://www.elfa.se/sv/led-565nm-groen-mm-kingbright-7113lgd/p/17510192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) | 2
| Red LED | @Future work Indicate Power Status of ECU | 1 | --- | [Link](https://www.elfa.se/sv/led-627nm-roed-mm-kingbright-7113lid/p/17501464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) | 2
| M3x10mm Screw | Screw Down Internal Components | 16 | --- | [Link](https://www.elfa.se/sv/skruv-uttagskapa-sexkant-mm-m3-10mm-paket-med-100-delar-bossard-bn-610-m3x10mm/p/30071964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) | ---
| M3x10mm Nut | Screw Down Internal Components | 14 | --- | [Link](https://www.elfa.se/sv/hex-nut-m3-m3-4mm-foerzinkat-stal-bossard-m6m-m3/p/14800070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) | --

### Interfacing with Hardware Interface and Low Level Software
The embedded software can interface with the hardware interface and low level software. Physically, this is done through a CAN bus network (D-Sub 9 connector between nodes). Software wise, a custom encoding and decoding CAN library has been implemented in C language. Onto this custom library, two software libraries have been created for autonomous platform generation 4.

The data sent over the CAN bus needs to be available on ROS2 topics in order for ROS2 nodes to be able to use the data in computations in the hardware interface and low level software. In the same way, actuator commands sent from ROS2 nodes on ROS2 topics need to be sent to the ECUs over CAN.

The CAN frames sent over the CAN network must be encoded and decoded correctly and in the same way on both the hardware interface and embedded ECUs. Therefore a unified CAN database file has been constructed for autonomous platform generation 4. A helper library is used to convert the CAN database file into a set of C-style data structs.

CAN communication information transportation illustration. 

CAN communication information transportation illustration. 

Two custom made libraries have then been implemented, one in the embedded software and one in ROS2 in hardware interface and low level software.

How to extend this functionality with new CAN frames and signals is explained in detail in `Hardware_Interface_Low_Level_Computer\HOW_TO_EXTEND.md`. (The parts that are relevant to change in hardware interface and low level software is documented here). How to extended the software for the embedded ECUs is described in `CAN_Nodes_Microcontroller_Code\HOW_TO_EXTEND.md`.

### Unified CAN Database
A unified CAN database has been created for autonomous platform generation 4. It uses the standardized .dbc file format and can be read/written to using commonly available softwares. I.e [Kvaser DBC editor](https://kvaser-database-editor.software.informer.com/2.4/).

The CAN library database file is located in `\CAN_Nodes_Microcontroller_Code\CAN_LIBRARY_DATABASE\CAN_DB.dbc`.

Every CAN bus frame and signal present on autonomous platform is defined in this file. This means when adding a new signal to the platform, it only has to be defined in one single file. 

With an external library (added as a git submodule to this repository) standardized C code can be automatically generated. A simplified interface to encode and decode CAN frames and signals is created. The library used can be found [here](https://github.com/howerj/dbcc). How to use it is described in `\CAN_Nodes_Microcontroller_Code\CAN_LIBRARY_DATABASE\README.md`

This CAN_DB.dbc (and autogenerated code from this file) can then be linked to various software components on autonomous platform generation 4. This is illustrated below.

CAN communication information transportation illustration.

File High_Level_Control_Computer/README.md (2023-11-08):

# High-Level Control Software
This directory contains the high level control software which is responsible for sending high level control commands to the low level control software. 

## High-Level Control Hardware Requirements 
To run the high-level control software it is preferable to run it on Linux. (Tested on Ubuntu 22.04). The processor should of x86 type. It is preferable to have a dedicated graphics card if one has to run a lot of digital twin simulations.

See physics simulator Gazebo Simulator hardware requirements [here.](https://se.mathworks.com/help/robotics/ug/gazebo-simulation-requirements.html)

To run high-level control on windows the docker graphics passthrough methodology needs to be modified. Currently it has only been setup for Linux. There will also be a greater performance loss when running a linux based docker container on windows compared to linux. 

The high level software is the highest level software layer, it is supposed to be hardware agnostic. It should not care what specific hardware is implemented on the physical autonomous platform. 

The high level control software is supposed to tell the autonomous platform WHAT to do, whilst the low level control software is supposed to tell the platform HOW it should do it. This means that the algorithms developed / used in high level control software can be transferred to any physical platform as long as there exists an interface for it.

As an example: A high level software component wants the platform to move forward. It relays this on a generic ROS2 topic (i.e /cmd_vel) to the low level software, the low level software then processes it and sends commands specific to the physical platform to the embedded software layer. The low level software would then output hardware specific commands over the CAN bus network.

High level overview 

Above is a schematic diagram of how the software in high level control software should be designed. As of August 2023 only a simple digital twin is implemented so far.

### How To Start

The high level software container should be started on the development laptop. NOT on the Raspberry Pi since it can not render the 3D gazebo simulation.

If any error occurs, `TEST_DEBUGING.md`, for troubleshooting.

Note: As of August 2023 it starts the digital twin software on ROS_DOMAIN_ID = 0 meaning it will not be able to interact with the physical platform even if the computers are located on the same wifi network. Hardware platform ROS2 network has ROS_DOMAIN_ID = 1.

Note: The host computer needs to be configured to pass graphical elements to the container. (before starting the container)

(Make sure your terminal path is located in this directory)

```bash
xhost +local:*
```

First, rebuild the container using 
```bash
docker-compose build
```

The high level software container, with the configurations, can be started using 
```bash
docker-compose up
```

The expected terminal output is:

Expected terminal output when starting the HLC docker container 

Two new windows should open up, Gazebo and Rviz, and will look something like this:

Expected graphical output when starting the HLC docker container 

The digital twin can be controlled (drive around manually) using the keyboard in a new terminal window.

Enter the running container
```bash
docker exec -it ap4hlc bash
```
Navigate to workspace, source environment variables
```bash
cd ap4hlc_ws
source install/setup.bash
```

Start tele-operation twist keyboard:

```bash
ros2 run teleop_twist_keyboard teleop_twist_keyboard
```

By using 'i', 'j', 'l', 'k' and ',' one can now control the digital twin.
See expected terminal output below.

Manual keyboard control of platform 

A running container can be stopped by either 'Ctrl+C' in the terminal in which 'docker-compose up' was run. OR in a new terminal:
```bash
docker stop ap4hlc
```

### Autonomous Driving Stack 

This has not been implemented as of August 2023.

In the future, the high level control software shall contain an autonomous drive stack. It would be the highest form of control software to the platform, taking in sensor data, processing it and deciding on an actuator output. There exists available AD driving stacks which one can use, i.e OpenPilot [(Link here)](https://github.com/commaai/openpilot). Hamid has previous experience with using OpenPilot. One could also develop some autonomous driving stack in-house or as a part of thesis project.

The idea would still be the same, sensor information and physical platform states would be received on standardized ros2 topics. The information would be processed in some ROS2 nodes and eventually the output would be a change of vehicle state. The output should follow ROS2 convention of controlling robots. I.e a new desired linear velocity and rotational velocity should be output on the `/cmd_vel` ROS2 topic.

For topic conventions see ROS2 topic message [Sensor Messages (link)]() and [Navigational Messages (link)]().

For quick reference

* (INPUT) Platform Odometry (Current position + Orientation) see ["/odom"](https://github.com/ros2/common_interfaces/blob/humble/nav_msgs/msg/Odometry.msg) 
* (OUTPUT) Velocity in 3D (linear + angular) [`/cmd_vel`](https://docs.ros2.org/latest/api/geometry_msgs/msg/Twist.html)
* (INPUT) Sensor readings. See common sensor topics [here](http://wiki.ros.org/sensor_msgs?distro=humble)

### Digital Twin

A simplified digital twin has been implemented as of August 2023.

An important part of the high level software control is the digital twin. It is a completely different component then the autonomous driving stack and should be agnostic to what AD stack is used. This means that any AD stack should be able to be tested on the digital twin. This is accomplished by using standard ROS2 topics as interfaces as briefly described in the previous section. Inputs to the digital twin would be sent over the `/cmd_vel` ROS2 topic, in the same way outputs (vehicle state and sensor readings) would be sent from the digital twin simulation over standard ROS2 topics. I.e "/odom" for vehicle state.

As of August 2023 the digital twin is run using the Gazebo Physics Simulator. [Link official gazebo documentation.](https://gazebosim.org/docs) It is a software that integrates seamlessly with ROS2 and has been used for a long time to simulate robots in complex environments. 

The code structure for the digital twin is as follows:
A ROS2 package has been created, autonomous_platform_robot_description_pkg, which contains the digital twin. 

```
 ┣  High_Level_Control_Computer
 ┃ ┣  ap4_hlc_code
 ┃ ┃ ┗  ap4hlc_ws
 ┃ ┃   ┗  src
 ┃ ┃      ┗  autonomous_platform_robot_description_pkg
 ┃ ┃         ┣  launch
 ┃ ┃         ┣  rviz
 ┃ ┃         ┣  src
 ┃ ┃         ┃  ┗ description
 ┃ ┃         ┃     ┣  ap4_robot_description.urdf
 ┃ ┃         ┃     ┣  gazebo_control.xacro
 ┃ ┃         ┃     ┣  gokart_chassi.urdf.xacro
 ┃ ┃         ┃     ┗  inertia_macros.xacro
 ┃ ┃         ┗  worlds
 ┃ ┃
 ┃ ┣   Dockerfile
 ┃ ┣   docker-compose.yaml
 ┃ ┗   README.md <-- You Are Here !!!
```

### Design Of Digital Twin
The digital twin of autonomous platform is created using Universal Robot Description Files (URDF) and xacro files. The digital twin is described in an xml type format and are located in `autonomous_platform\High_Level_Control_Computer\ap4_hlc_code\ap4hlc_ws\src\autonomous_platform_robot_description_pkg\src\description\`. 

These files describe everything from the physical platform properties to what sensors are simulated. How the platform is controlled can also be configured. The end result can be seen below, a simplified gokart platform with wheels that can be controlled.

RVIZ 

### Sensor plugins
An important aspect of using Gazebo is the concept of plugins. Plugins allows for new functionality to be added to the digital twin. For example different vehicle movement controllers or virtual sensors.

As of August 2023 no sensors have yet to be added. Future sensors to add could be:

* [Camera](https://classic.gazebosim.org/tutorials?tut=ros_gzplugins)
* [Lidar](https://classic.gazebosim.org/tutorials?tut=ros_gzplugins)
* [Radar](https://classic.gazebosim.org/tutorials?tut=ros_gzplugins)
* [IMU](https://classic.gazebosim.org/tutorials?tut=ros_gzplugins)
* [Ultrasonic short range sensor](https://classic.gazebosim.org/tutorials?tut=ros_gzplugins)

### Gazebo worlds
In the same way as the digital twin could be configured, the simulated environment itself can be configured. This allows a developer to create interesting scenarios in which to place the autonomous platform.

Worlds can be created using the Gazebo graphical application and saved into the `worlds` directory. The digital twin can be configured to start in a specific world by configuring the launch file located in `launch` directory.

Gazebo has access to an exentsive library of 3D models which can be used to crate interesting environments. 

Example Gazebo world top view 

Example Gazebo world 3D view 

### Software Control Switch

This has not been implemented as of August 2023.

The idea of having a software control switch is for the autonomous driving stack algorithms to EITHER control the physical platform or the digital twin. And be able to switch seamlessly between them. The autonomous driving stacks could be quickly tested on a digital twin to make development faster and when the algorithms are in a mature state they could be tested on the physical platform.

It is therefore very important that the digital twin and physical platform have the same output (sensor readings / vehicle state). I.e on the same ROS2 topics. In the same way, the digital twin and the physical platform should be controlled in the same way in the high control software on `/cmd_vel` topic.

For future reference this switching of control could be actualized using [namespaces](https://docs.ros.org/en/foxy/Tutorials/Intermediate/Launch/Using-ROS2-Launch-For-Large-Projects.html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) or configuring different [ROS2 domain IDs](https://docs.ros.org/en/foxy/Concepts/About-Domain-ID.html). By setting the ROS2 DOMAIN ID for the AD nodes to the same ID as the physical platform commands would be forwarded to the low level software control. And by setting a different domain one could ensure that the commands are only sent between the digital twin and AD algorithms. ROS_DOMAIN_ID is specifically developed to prevent cross talk between different domains.

### Digital Twin Software Package Structure
The software for the digital twin is located in `autonomous_platform_robot_description_pkg`. Below follows a quick guide on what each subdirectory contains:

* launch - Contains launch files
* rviz - contains a parameter file which can be inserted into Rviz to show useful information upon startup
* worlds - save gazebo simulation environments (worlds) to be run later.
* /src/description: Contains the xacro and urdf files which describes how the digital twin is built up.

The launch file launch_digital_twin_simulation.launch.py launches the following nodes

* robot_state_publisher
* Rviz
* gazebo_node
* spawn_entity_node

The robot state publisher node, takes the robot description files and broadcasts them over the ROS2 network. The Gazebo physics simulator is then launched with a corresponding ROS2 node. Lastly, a spawn entity node is created, which spawns the digital twin inside the gazebo simulation using the information on the robot state publisher information topic. As the digital twin is inserted into the simulation, it spawns further nodes which makes it possible to control the digital twin using the /cmd_vel topic.

The digital twin is defined inside the description folder, it is built in modules with the ap4_robot_description.urdf as a base. Onto this base. The gokart_chassi.urdf.xacro describes the kinematics and dynamics of AP4. gazebo_controls.xacro describes how an ackermann drive plugin is used to control the joints of AP4.

Future sensors, such as cameras, should be added as xacro modules and included in the ap4_robot_description.urdf file.

### How to Connect to Physical Platform

The high-level control software is meant to be run in two modes; connected to the autonomous platform and completely detached.

The long term goal is that the high level control software should be able to interface with the low level control software running on the Raspberry Pi 4b. This is done through an ethernet connection, meaning it could be done both wirelessly and by wire. The two docker containers for high level software and low level software should therefore be started from devices located on the same network.

As of August 2023 this is NOT needed yet, since no Autonomous Driving algorithms have been implemented yet. But for future reference:

* Connect the development laptop to the AP4-ROUTER_2.4Ghz network. ssid and pw credentials can be found in root directory README file.
* Make sure the two docker containers are started
* Make sure high level software is running on ROS_DOMAIN_ID=1

This should be sufficient for the underlying ROS2 Data Distribution Service (DDS) to find ROS2 nodes available on the same network and same ROS_DOMAIN_ID.

### How to verify

If any error occurs, `TEST_DEBUGGING.md`, for troubleshooting.

### High Level Control Underlying Software Components 
This section will describe what software components are used to construct the high level software and how they are used.

### Containerization 
An overview of containerization and how it works is explained in `SOFTWARE_DESIGN.md` located in root directory.

Note: Docker can be run on Windows, but certain commands/parameters used on AP4 are linux specific. I.e passing graphics to and from the container. It is has therefore only been tested and guaranteed to work on linux host computers.

Docker enables software to be collected and run from a virtual environment, similar to a virtual machine but with much less performance overhead compared to a virtual machine. Docker allows the virtual environment to be configured, i.e what operating system should be run and what software should be installed.

The environment in which the high level software is run in is described inside the `Dockerfile` located in this directory. In this file the virtual environment is configured as a base version of Ubuntu 22.04 with relevant linux packages installed. Robot Operating System 2 - Humble is installed.

The container is started using a set of configuration parameters, these are located in `docker-compose.yaml` in this directory. Configuration parameters can be for example to pass through graphical elements from the container to the host computer desktop.

### Robot Operating System 2 (ROS2) 
Robot Operating System 2 (ROS2) is a framework / middleware developed to create very complex robotic software. This framework is used to split up computations into separate executions using "nodes". 

For an in depth explanation of Robot Operating System 2 (ROS2) and how it works see `SOFTWARE_DESIGN.md` in root directory.

The following subsection will describe how the high level software control is designed using the Robot Operating System Framework.

The idea with using ROS2 framework is that computational applications can be split up into smaller components that perform very specific tasks. I.e software related to taking a joystick input and outputting a desired velocity should have the minimum amount of dependencies as possible and not break any other dependencies for other software applications.

ROS2 package has to be created for this functionality. A package collects all the resources and dependency configurations for a specific function. I.e the package for the digital twin `autonomous_platform_robot_description_pkg` should be as standalone as possible. When adding future functionality, the digital twin package should be left as is, and instead a new package for the new specific functionality should be added.

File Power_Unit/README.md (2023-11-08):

# Power Module

The power consumption of the implemented AP4's hardware has been calculated in  the table below. The values have been derived from each component's product manual, which can easily be found on the internet. The values are based on the nominal values in order to define overall power consumption. Some components have been neglected such as the losses in cables, wires and switches. The power calculation follows the well-known electrical direct current power formula: `P = U . I [W]` where `U` is the voltage and `I` is the current.

| Component | Voltage  | Current  A | Quantity | Power W |
|---|---|---|---|---|
| Raspberry Pi 4b | 5 | 1.01 | 1 | 5.1 |
| DC-Motor EMG49 | 24 | 2.1 | 1 | 50.4 |
| Cooling Fan | 12 | 0,095 | 2 | 2.28 |
| Bluepill | 5 | 0.035 | 1 | 0.175 |
| MCP2515, CAN module | 5 | 0,05 | 1 | 0,25 |
| MCP4725, DAC | 5 | 0,05 | 2 | 0,05 |
| Router | 12 | 1 | 1 | 12 |
| Camera, Logitech c920 | 5 | 0.5 | 1 | 2.5 |
|  |  Total Power Consumption: | 73.2 |

The power module consists of three components, a battery, a battery charger and a power supply unit (PSU). Furthermore, there is a user interface including a power switch, emergency kill switch and outlets that select which power source that should be used for the autonomous platform. Also, there are voltage- and current measurement units mounted, but they are not implemented in software or physically connected to an ECU. The complete electrical circuit of the power module and a rendered illustration of the CAD files for the power module can be seen in here:

Power in to AP4 out flow described in a electrical circuit. Including voltage sensor, current sensor, switches for power on and emergency stop killing all the power in AP4.

Battery supply to the outlet Battery out flow described in a electrical circuit. Including voltage sensor, current sensor, fuse and emergency stop killing all the power in AP4.

![Rendered illustration of the Power module. The main component is the battery holder (red) to which the remaining components are mounted to. The battery holder holds the lead acid battery. The battery charger (yellow) is mounted onto the side. A PSU module (green) is mounted to the side. The power module interface (green) is mounted on top of the battery holder, providing an interface to the power module. An emergency stop, on switch and power connectors.](Resources/powr_module.png) 

### Battery and Charger

The battery chosen is a 12 V lead acid battery from Biltema. The battery is typically used for lawnmowers and similar machines. The corresponding battery charger selection is based on compatibility with the battery, also from Biltema. The battery capacity is 30 Ah and weighs about 8kg. Thus from the derived system current consumption the theoretically run-time of the system will be:
`t = 30/8.33 = 3.6 hours` 

Having a power supply unit (PSU) connected to the electrical grid will enable the use of AP4 in a controlled environment. This can be done inside of a lab with the AP4 raised, so no wheel contact on the surface. Thus enabling the testing of higher levels of algorithms without the movement and unnecessary use of the battery that will shorten its lifespan. 

### User interface

The electrical circuit for the user interface and connected sensors and the schematic of the power module can be seen in the images below. The user interface includes three different outlets in order to select which power source that should be used. These outlets are called,  battery out,  power in,  AP4 out.  Battery out is directly connected to the battery terminals, with the kill switch in series.

Illustration of the power module top interface. Showing the three different power connectors, AP4 OUT, POWER IN and BATTERY OUT. The Emergency kill switch and power switch is also illustrated. The PSU and battery charger and their respective power connector is shown in the bottom om the figure. 

 Power in outlet will power the whole platform. The  power in is connected to the kill switch, power switch and fuses, then passed out to  AP4 out that is connected to the rest of AP4. The selection of power source is based on which source either PSU or battery is connected to the  power in outlet. For example, the PSU could power the platform whilst the battery is charged at the same time.

Side view of power module component. A Power Supply Unit (PSU) is mounted to the side. It enables the platform to be powered through a wall socket.

Top view of the power module component. On the top a user can configure how the platform should be powered. An E-stop and flip switch in wired in series allows users to turn on and off the platform.

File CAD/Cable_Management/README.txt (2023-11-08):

Cable management - sort them out snapper 3DCR by Prenta on Thingiverse: https://www.thingiverse.com/thing:122600

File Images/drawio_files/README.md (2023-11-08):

# Draw.io files

.io files can be opened in a web broswer using [link](https://app.diagrams.net/).

This a very useful tool to quickly illustrate, draw diagrams and program flow. A drawio file can contain many sub-sketches.

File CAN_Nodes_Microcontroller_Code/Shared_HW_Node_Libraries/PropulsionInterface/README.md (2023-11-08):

# Shared libraries

lib_deps = 
	autowp/autowp-mcp2515@^1.0.3 
    SPI
	Wire
	adafruit/Adafruit MCP4725 @ ^2.0.0
	adafruit/Adafruit INA219 @ ^1.1.1
    adafruit/Adafruit BusIO @ ^1.9.3

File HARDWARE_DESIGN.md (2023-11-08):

## Hardware Design Principles
This document aims to collect the design principles for any new hardware added. Hardware may need to be added for different software layers, hence they can be summarized here.

See `HOW_TO_EXTEND.md` for general design principles. These should always be kept in mind.

### Modular Mounting of Components

This document is supposed to collect our thought about how sensors, hardware and components should be mounted on autonomous platform in order to make it as modular and adaptable as possible for future use.

### General idea
Use a metal sheet with pre fabricated metal holes as a base for mounting components. Create 3D printed fixtures to connect Hardware Nodes, Raspberry Pi 4 and other major components.

Layout 

Using the prefabricated holes one can then create 3d printed fixtures in a standardized way to mount hardware anywhere along the sheet.  

Mounting idea 

Component mounting 

Specific solutions for this needs to be CADed later on.

### Mounting the aluminum plates to the frame

One can either use the pre existing mounting holes on the gokart chassis and screw directly into the chassis.

Pre existing mounting holes on the gokart chassis 

Or one can create 3d printed fixtures to mount the plates, I.e:

3d printed fixtures 

### Component list

* Aluminum metal sheet with be fabricated holes: Aluminum Lochblech blank 250x500x1.5mm article nr:  148-21-919 OR 4001116378041  https://www.elfa.se/en/aluminium-perforated-plate-round-holes-500x250x1-5mm-alfer-4001116378041/p/14821919 Holes are spaced 15 mm apart, hole diameter 4.5 mm

Aluminum sheet 

* M4 machine screws
* M4 nuts

One can either use pre existing cable routing hardware as in the image below

Pre existing cable routine 

 or can 3d print simple cable holders such as this image 

3d print simple cable holders 

3d print simple cable holders

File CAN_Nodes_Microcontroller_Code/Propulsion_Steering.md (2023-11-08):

## Steering Propulsion Control Unit (SPCU) 

The implemented SPCU follows the structure and base mentioned in previous chapters. In the figure below is the circuit and schematic of the components used. Each module has a designated sw library located at: */Shared_HW_Node_Libraries*. Below is a table of specific added modules for SPCU.

| **Component** 	| **Purpose** 	| **Documentation Repo Paths** 	|
|:---:	|:---:	|:---:	|
| MCP4725 	| Translates PWN voltage signals to Analog. In order to simulate the pedal voltages (0.8-4.3 V) 	| `*\Documentation\Segway_Propulsion\Manuals*` 	|
| Sabertooth Kangaroo x2 	| Serial communication to send motor commands. SI interface and utilizes the limit switches. 	| `*\Documentation\Steering_Motor\manuals*` 	|
| Sabertooth dual motor driver 	| Motor driver to control the DC motor used for steering, feedback with the built in encoder. 	| `*\Documentation\Steering_Motor\manuals*` 	|



Above is a rendered illustration of the SPCU, with its corresponding modules used for steering and propulsion. Down is a flowchart of the software used for the SPCU. The median run-time of the main-loop is 3 ms. Thus passing the requirement of 20ms for real-time systems.



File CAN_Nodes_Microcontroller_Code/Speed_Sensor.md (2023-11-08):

## Speed Sensor ECU

These are diagrams that describe the physical wiring of the speed sensor module. The design files are in the 
[diagrams](../Documentation/Speed_Sensor/diagrams) directory and can be edited. The diagram tool is diagrams.net, while the circuit diagram is made with EasyEDA online.

### Functional block diagram

ECU - speed sensor block diagram

### Wiring overlay

This is an overlay of the components in the circuit.

ECU - speed sensor block diagram

### Circuit diagram

This is a complete representation of the how the ECU and its components are wired internally.

ECU - speed sensor circuit diagram

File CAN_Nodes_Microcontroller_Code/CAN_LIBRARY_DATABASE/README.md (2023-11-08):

### Controller Area Network Database

The way of working with CAN database for AP Gen 4 is illustrated below. Using a database in dbc format being parsed through the script from howerj repo (see below), that is producing a csv file and cpp file with functions to use to encode and decode messages. Thereafter it is included to all control units that is communicating over the CAN buss system.



### dbc editor
There are several different softwares that can be used. One example is https://kvaser-database-editor.software.informer.com/2.4/, which is free to download. It is very intuitive to use and build up dbc files, a example can be seen below. Where the frames and signals is defined for the Steering, Propulsion control unit (SPCU). To the right the bit's position in the messages is illustrated, however one important note is that the editor don't check if some signals overwrite each other!



Below is an detailed description of the commands used.

### How to use DBC to C library

The dbc to c (dbcc) repository is added as a submodule. 

If the dbc_to_c folder does not show up as a directory, init and update repository submodules with

```bash
git submodule init
git submodule update
```

Link to repository for documentation: https://github.com/howerj/dbcc 

Make sure the library is built using 'make'
move into the c_to_dbc directory and write

```bash
make
```

If 'make' does not work, try running the following two commands first to make sure that it is installed.

```bash
sudo apt update && sudo apt upgrade -y
sudo apt install -y make
```

The command 'make' also requires the GNU C compiler (gcc) to be installed. Run the following command to install the compiler/to confirm that it is installed.

```bash
sudo apt install gcc
```
If make has run properly, a new file called dbcc, should then appear inside the dbc_to_c folder.

Lastly, simply exit the dbc_to_c folder and run the .sh file as following:

```bash
./create_database_from_dbc_script.sh
```

For additional debugging:

* Parse ex1.dbc to a .c and .h file to a directory called output_dir:
```bash
./dbcc -v -o output_dir ex1.dbc
```
In output_dir two new files should appear, ex1.c and ex1.h

* Parse ex1.dbc to csv file to a directory called output_dir:

```bash
./dbcc -C -v -o output_dir ex1.dbc
```
A ex1.csv file should appear in the output_dir

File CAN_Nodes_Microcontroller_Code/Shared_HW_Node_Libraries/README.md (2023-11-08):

## Shared libraries

This folder is meant to collect libraries shared by multiple hw nodes.

These can then be used by multiple platformIO projects by including the path in the platform.ini file for the active project.

### Structure of shared library
The structure of a shared library shall be split into two parts, the code itself located in the **src** directory and a documentation folder **documentation_and_research**:

```bash
  shared_library_example
 ┣  src : Contains the code that is imported into projects.
 ┃ ┣    some_code.cpp
 ┃ ┣    some_code.h
 ┃ ┗    ....
 ┃
 ┗  documentation_and_research : Contains relevant documentation for the code presented in a .md README file
   ┣   Images (Optional)
   ┣   Manuals (Optional)
   ┣   Test_rig_code (Optional) : Contains any related code that
   ┗    README.md
   ┃  
   ┣   SPCU
   ┗   README.md
```

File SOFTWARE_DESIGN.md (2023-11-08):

##  Software Components
The procedure of installing some software will be mentioned in this section.
You need:

* Preferably have a linux based computer if you want to run code.
* If you only want to read through the documentation, staying in the browser is sufficient.
* OR if you only want to download and look through the repository a Windows host computer is sufficient.

### Information and Background
This README file is meant to collect information about all the software components used to construct Autonomous Platform Generation 4 or any tools used in this project. A lot of Software is used both in `Hardware_Interface_Low_Level_Computer` and `High_Level_Control_Computer`, and instead of explaining the same thing twice it can be collected here. It will also give new members of the project a structured document to read through.

This is meant to give new members a quick overview and explain the most important concepts related to the autonomous platform project.

The software and components that will be described in detail in this document are

* [VSCode](#VSCode) IDE
* [Linux Ubuntu 22.04](#linux-ubuntu-2204)
* [Git](#Git)
* [Containerization](#Containerization)
* [Robot Operating System 2 (ROS2)](#Robot-Operating-System-2-(ROS2))
* [PlatformIO & VSCode]()
* [Jenkins]()

### IDE 
The recommended Integrated Development Environment (IDE) is Visual Studio Code (VSCode). It is a free versatile IDE with many useful plugins. The built in file explorer makes navigation of the AP4 repository very easy.

See installation guide [here](https://code.visualstudio.com/) for Windows / Linux.

Visual Studio Code supports the use of plugins, referred to as extensions. These can be installed simply inside VSCode by navigation to the extensions tab. (Tab with four small squares to the left)

The recommended list of extensions are:

* C/C++
* Python
* PlatformIO

### Linux Ubuntu 22.04 
The project software is meant to be run on Linux Ubuntu 22.04, therefore it is good to have basic understanding on how to use linux. (Good ability to google linux commands and copy paste commands is recommended!)

A linux for beginners guide related to development using Robot Operating System Framework can be found [here](https://www.theconstructsim.com/robotigniteacademy_learnros/ros-courses-library/linux-for-robotics/). It is an online interactive tutorial suitable for a project member which has NEVER worked in linux before. If you know how to navigate using the linux terminal and copy paste commands, skip this!

### Git 

Autonomous Platform Generation 4 uses the "MonoRepo" mantra. Everything related to AP4 is collected inside ONE repository called `autonomous_Platform_Generation_4`. If you manage to clone this onto a computer you have everything you need to get started.

Installing Git through command line is preferred. See the official guide [here](https://git-scm.com/book/en/v2/Getting-Started-Installing-Git) and choose appropriate operating system. Running the code has not been tested on Windows machines but it is still possible to read through the documentation and inspect files on  a Windows device.

### Containerization 
The High level and low level software runs inside a docker containers (on the Development laptop and Raspberry Pi 4b). [Official Docker Page](https://docs.docker.com/get-started/overview/). It is similar to a Virtual Machine, in that it can run software in a separate compartment from the host computer software. It does not take up as much resources as a VM and is much faster to spin up (start). Docker containers uses the following components to create containers.

Docker file 

Dockerfile: [Dockerfile Official Documentation](https://docs.docker.com/engine/reference/builder/). A dockerfile is a text file describing the software environment which will be run in the container. For example, running Ubuntu as a base with with X,Y standard linux packages installed onto it. So every library or package one would install on a linux desktop version, one could define in this file. This dockerfile can then be built into a docker image. (everytime a container is rebuilt, anything saved in it is LOST). See `Hardware_Interface_Low_Level_Computer/dockerfile` for an example of a dockerfile.Therefore software should be written outside the container and passed into the container through volumes. See `Hardware_Interface_Low_Level_Computer/docker-compose` how this is performed by mounting volumes.

A docker image can then be spun up which creates a container.

A container can be spun up with several configurations commands. [List of commands](https://docs.docker.com/engine/reference/commandline/run/). For example, it is possible to mount volumes (directories) into the container.

#### Installation of Docker
See official guide [here](https://docs.docker.com/engine/install/) Choose appropriate operating system.

As of August 2023 AP4 containers have only been configured to run on a Linux Host computer.

### Containers

The containers for autonomous platform contains two docker related files, __dockerfile__ and __docker-compose__. The dockerfile describes the software environment (ubuntu 22.04 Jammy) with additional software and onto this the ROS2 framework and additional libraries are installed. The docker-compose file uses the dockerfile to launch a container with a set of parameters. For example, passing in and out graphical elements, and passing created software (as a directory) (performed by mounting a volume) into the container. In the docker-file a command which runs when starting the container can be defined. This can be useful to call a startup script that would run inside the container when starting it. This is done using the command: keyword.

Note: Docker can be run on Windows, but certain commands/parameters used on AP4 are linux specific. I.e passing graphics to and from the container. As of August 2023 it is therefore only possible to run the high level software on linux. See 'FUTURE_WORK.md' for instructions on how to possibly solve this issue.

The container, with the configurations, can be started using: (Terminal path has to be located in the directory where the dockerfile and docker-compose is located at) 
```bash
docker-compose up
```

Note: The host PC needs to be configured to pass graphical elements to the high level computer container. (before starting the container)
```bash
xhost +local:*
```

It is possible to enter a running container environment using
```bash
docker exec -it <container-name> bash
```
Running containers can be listed using 
```bash
docker container ps
```

A running container can be stopped by either 'Ctrl+C' in the terminal in which 'docker-compose up' was run. OR in a new terminal:
```bash
docker stop <container-name>
```

### Robot Operating System 2 (ROS2) 
Robot Operating System 2 (ROS2) is a framework / middleware developed to create very complex robotic software. The first version was released around 2007 and its successor, ROS2 was released around 2019. The version used for AP4 is ROS2-humble. [ROS2 Humble Docs](https://docs.ros.org/en/humble/index.html). ROS2 Humble has an End of Life (EOL) of [2027](https://docs.ros.org/en/humble/Releases.html). Future work should still use Humble as it has the most availible packages. Different distributions of ROS are NOT compatible. In theory it is possible to bridge a ROS1 distribution with a ROS2 distribution using ROS bridge if a package does not exist for ROS2, this is not implemented on AP4. [ROS bridge link](https://industrial-training-master.readthedocs.io/en/melodic/_source/session7/ROS1-ROS2-bridge.html)

ROS2 has tier 1 support for Linux Ubuntu 22.04. And tier 3 support for Linux 20.04, on autonomous platform generation 4 Ubuntu 22.04 is used.

ROS2 applications can be written in either C++ or Python. There are tutorials for both versions. Different nodes (Computational applications) written in separate languages can still communicate with another using the ROS2 API & Framework. Therefore, use what programming language you are most comfortable with. In applications where execution speed is of outmost importance, using C++ can be preferred. But for testing new concepts or developing high level control algorithms Python is more than sufficient. Even if something is written in Python it still has to be compiled into a ROS2 package before it can be run.

#### ROS2 Useful commands quick reference
A common methodology to debug software written for the ROS2 framework is to observe the behavior through a terminal window. Here is a list of useful ROS2 commands for quick reference in the future.

#### Commonly used commands to debug
Source underlying ros2 environment variables
```bash
source /opt/ros/humble/setup.bash
```

Sourcing environment variables specific to a workspace (open terminal in workspace directory)
```bash
source install/setup.bash
```

List what topics are currently being broadcasted to on the ROS2 network.

```bash
ros2 topic list
```

Read in thermal what is broadcasted onto a specific topic
```bash
ros2 topic echo ${topic_name}
```

Publish data onto a specific ros2 topic. If environment variables are sourced tab autocomplete works.
```bash
ros2 topic pub ${topic name} ${message type} ${message data}
```

List active nodes on ROS2 network
```bash
ros2 node list
```

Display useful information about a specific node.
```bash
ros2 node info ${node name}
```

#### Visualization
Visualize the ROS2 network of nodes and topics in a GUI.
```bash
ros2 run rqt_graph rqt_graph
```

Plot data sent over different topics. Useful for I.e plotting requested velocity vs measured velocity to debug system and observe behavior. Any numerical data sent over a topic can be plotted.
```bash
ros2 run rqt_plot rqt_plot
```

#### Saving data sent on topics
Save topic information transmitted over the ROS2 network. [Documentation here](https://docs.ros.org/en/foxy/Tutorials/Beginner-CLI-Tools/Recording-And-Playing-Back-Data/Recording-And-Playing-Back-Data.html). Record what is transmitted over a specific topic (Ctrl + C to stop recording):
```bash
ros2 bag record -o ${your bag file name} ${topic name 1} ${...} ${topic name n}
```
Display information regarding the bagfile that was previously recorded
```bash
ros2 bag info ${bag file name}
```
To record all information sent over all topics in the ROS2 network
```bash
ros2 bag record -o ${your bag file name} -a
```
The information recorded can be played back and will be outputted to the ROS2 network on the same topics that they were recorded on, using:
```bash
ros2 bag play ${bag file name}
```

#### Available ROS2 Resources 
Here are resources on ROS2 which can be useful for future work.
* Beginner level [Interactive ROS2 tutorial](https://www.theconstructsim.com/robotigniteacademy_learnros/ros-courses-library/ros2-basics-course/) with online excercies. VERY USEFUL

*  Beginner Tutorial: [Writing a simple publisher and subscriber (Python)](https://docs.ros.org/en/foxy/Tutorials/Beginner-Client-Libraries/Writing-A-Simple-Py-Publisher-And-Subscriber.html)
* Beginner Tutorial: [Writing a simple publisher and subscriber (C++)](https://docs.ros.org/en/foxy/Tutorials/Beginner-Client-Libraries/Writing-A-Simple-Cpp-Publisher-And-Subscriber.html)
* [ROS_DOMAIN_ID](https://docs.ros.org/en/humble/Concepts/About-Domain-ID.html)
* [ROS2 Interfaces](https://docs.ros.org/en/humble/Concepts/About-ROS-Interfaces.html) Fields and datatypes in ROS2 topics.
* [Official How-to Guides](https://docs.ros.org/en/humble/How-To-Guides.html) For common problems when developing software in ROS2 framework.
* [ROS2 On Raspberry Pi](https://docs.ros.org/en/humble/How-To-Guides/Installing-on-Raspberry-Pi.html) @TODO MOVE THIS POINT TO LOW LEVEL SOFTWARE
* [API Documentation](https://docs.ros.org/en/humble/API-Docs.html)

Here is a hands on video series on how ROS2 was used to create a mobile robot and a digital twin. It goes through the basics and then moves on to cover the advanced aspects of ROS2.  [Link - Articulated Robotics](https://www.youtube.com/watch?v=2lIV3dRvHmQ&list=PLunhqkrRNRhYYCaSTVP-qJnyUPkTxJnBt) Many of these concepts are used on Autonomous Platform Generation 4. 

#### ROS2 Concepts 
There are a few concepts which are very important to understand in order to understand how the high-level software is constructed on AP4. The official ROS2 documentation is a useful tool [ROS2 Beginner: CLI tools](https://docs.ros.org/en/humble/Tutorials/Beginner-CLI-Tools.html).

#### Node
[ROS2 Nodes official Documentation](https://docs.ros.org/en/humble/Tutorials/Beginner-CLI-Tools/Understanding-ROS2-Nodes/Understanding-ROS2-Nodes.html)

ROS nodes 

Nodes are where the software applications are written. Each node can be seen as a program (written in C++ or Python) performing some task. Weather it be processing information or interfacing with some hardware/software component. A node can perform multiple tasks and supports parallelization if configured correctly. [See Execution Management](https://docs.ros.org/en/humble/Concepts/About-Executors.html)

ROS node graph 

Nodes can communicate with other nodes using Topics, Services or Actions. This means sending information between them using a standardized communication interface. It is up for the developer to structure how information should be received and sent from nodes. This is done in the nodes themselves.

The communication between different ROS2 components on a network uses [DDS Middleware.](https://docs.ros.org/en/foxy/Concepts/About-Different-Middleware-Vendors.html)

#### Topic
[ROS2 Topic Official Documentation](https://docs.ros.org/en/humble/Tutorials/Beginner-CLI-Tools/Understanding-ROS2-Topics/Understanding-ROS2-Topics.html)

ROS publisher subscriber 

Topics are the means in which different Nodes can send and receive specific information. Information can be broadcasted using publishers and listen to using subscribers. These communication channels are called topics, each topic contains a topic name and a data field. The topic name determines what channel it will be sent over and the data field contains the information itself.

[List of generic built in topic data types](https://docs.ros.org/en/humble/Concepts/About-ROS-Interfaces.html). Custom data field types, containing multiple values sent in a single message can be created by a developer. [Link how-to](https://docs.ros.org/en/crystal/Tutorials/Custom-ROS2-Interfaces.html)

    Topic name
        data

Topics are broadcasted over the whole ROS2 network by publishers, meaning any other Node on the network can listen to any publisher. In order to direct data to a specific node, a developer must create a subscriber in the desired node, which listens to the correct topic name.

Note: There exists multiple [Quality of Service](https://docs.ros.org/en/rolling/Concepts/About-Quality-of-Service-Settings.html) parameters which can be configured. These can tell the DDS middleware what topics should be priotized when sending over the ROS2 framework. As of June 2023 these are set as standard priority. 

#### Services

[ROS2 Services Official Documentation](https://docs.ros.org/en/humble/Tutorials/Beginner-CLI-Tools/Understanding-ROS2-Services/Understanding-ROS2-Services.html)

ROS service 

Services work much like the topics, but there is a key difference. a node can request information (structured as a topic) from one node, and is guaranteed to receive information back.

Request functionality has to be created by the developer and is not something that is automatically built into a node. See tutorial [C++](https://docs.ros.org/en/foxy/Tutorials/Beginner-Client-Libraries/Writing-A-Simple-Cpp-Service-And-Client.html), [Python](https://docs.ros.org/en/foxy/Tutorials/Beginner-Client-Libraries/Writing-A-Simple-Py-Service-And-Client.html)

#### Actions
[ROS2 Actions Official Documentation](https://docs.ros.org/en/humble/Tutorials/Beginner-CLI-Tools/Understanding-ROS2-Actions/Understanding-ROS2-Actions.html)

ROS action 

#### Launch files
A launch file can be run in order to start several nodes at the same time. Launch files from existing packages can be called from within a launch file. 

[ROS2 Documentation: Creating a launch file](https://docs.ros.org/en/foxy/Tutorials/Intermediate/Launch/Creating-Launch-Files.html). 

[Call launch files from inside launch files](https://answers.ros.org/question/306935/ros2-include-a-launch-file-from-a-launch-file/)

#### Creating a ROS2 software package
In ROS2 a package is a form of library with functionality. Software inside a package is related to one function, therefore ROS code is very decentralized. This is very useful since existing packages can started separately and mixed together depending on application needs. Existing software packages can run parallel with custom user developed plugins to create new functionality. New packages can also be built on top of existing packages by defining dependencies.

A package can contain code for several nodes. So it does NOT have to be one node per package.

See a list of available ROS2 (version = Humble) packages [here](https://index.ros.org/packages/page/1/time/). Make sure filter is set to 'Humble'.

#### Structure of a ROS2 package
The file structure of a ROS2 workspace is standardized and can look something like like this: (don't worry most of the files in a package are automatically generated). All created packages are stored in the 'src' directory in the ROS2 workspace folder. Packages written in Python and C++ differ somewhat in content. Below is illustrated how to packages, one written in C++ and one written in Python are located in the filesystem.
```
 ┗  ros_ws
    ┗  src
        ┣ example_pkg_1 (C++) 
        ┃    ┣  launch (Optional)
        ┃    ┣  src
        ┃    ┃  ┗    <CODE>
        ┃    ┃  
        ┃    ┣   CMakeLists.txt
        ┃    ┗   package.xml
        ┃
        ┗  example_pkg_2 (Python)
             ┣  launch (Optional)
             ┣  resource
             ┣  test
             ┣  example_pkg_2
             ┃  ┣  __init__.py
             ┃  ┗   <CODE>
             ┃
             ┣    package.xml
             ┣    setup.cfg
             ┗    setup.py
```

#### Creating a ROS2 package
The official ROS2 guide can be found [here](https://docs.ros.org/en/foxy/Tutorials/Beginner-Client-Libraries/Creating-Your-First-ROS2-Package.html). The steps are summarized below. Packages can EITHER use CMake or Python depending on what programming language you want to use. You cannot mix programming languages within a package.

In order to create a package you need to be located inside a ROS2 workspace. For autonomous platform 4 this has already been setup. For curious members the documentation on how to create a ROS2 workspace can be found [here](https://docs.ros.org/en/foxy/Tutorials/Beginner-Client-Libraries/Creating-A-Workspace/Creating-A-Workspace.html).

### PlatformIO & VSCode 
PlatformIO is a Visual Studio Code (VSCode) extension.

In order to program the STM32F103C8T6 (Bluepill) microcontroller used for the embedded software a software driver is needed.

**Windows:**  
STSW-LINK009.
ST-LINK, ST-LINK/V2, ST-LINK/V2-1, STLINK-V3 USB driver signed for Windows7, Windows8, Windows10

Driver can be downloaded [here](https://www.st.com/en/development-tools/stsw-link009.html). It enables a windows computer to use the ST-Link v3 programmer which is used to program the bluepill microcontroller boards.

## Project standards and conventions

### Git commit messages
The project is using [conventional commits](https://www.conventionalcommits.org) as a commit standard meaning the commit messages are structured using the following standard:

```bash
<type>[optional scope]: <desription>

[optional body]

[optional footer(s)]
```

Types can be found under the summary section on [https://www.conventionalcommits.org](https://www.conventionalcommits.org).

Each section should be separated with a blank line.

The footer **SHALL** contain the Azure task ID using the following format `Azure-ID: xxxx`.

With conventional commits, a version can automatically be determined and assigned based on the "type" of commit made. The version follows the [Semantic Version (SemVer)](https://semver.org) specification.

### Merge commits
When merging locally the commit message will be declined by the commit-msg git hook. This can be overwritten by using the `--no-verify` option. In PyCharm this can be found by:
1. Navigating to the `Git` menu
2. Clicking on `Merge`
3. Clicking on the `Modify options` dropdown and selecting the `--no-verify` option

### Documentation 

Documentation is done in a markdown file. Try to keep our documentation close to your code. Keep the documentation short and clear. 

- `#` : Only used once for the tile of the project
- `##` : usually once in each markdown file and usually share semantic with the markdown filename.
- `###` : Different topics, try to split your documentation into at least 4 topics
- `####` : sub topics. Try to avoid when you can use simple paragraphs

## Automated Testing (CI/CD)

This document aims to describe how various software components on AP4 could be tested in jenkins. As of August 2023 no tests are implemented, instead this document collects useful links and resources that might lead to future automated software tests.

There are three layers of software that needs to be tested:

* Embedded Software in ECUs : Uses PlatformIO environment / framework
* hardware interface and low level software : Uses ROS2 framework
* high level control software and digital twin : Uses ROS2 framework

### Resources for automated testing of ROS2 software - Jenkins

* [Jenkins Basic for Robotics](https://app.theconstructsim.com/courses/jenkins-basics-for-robotics-77/) Online course on how to test ROS software using Jenkins
* [How to setup the Jenkins master](https://docs.ros.org/en/eloquent/Contributing/CI-Server-Setup.html) for ROS (note outdated version of ROS but should exist similar for newer version)

### Resources for automated testing of embedded software platformio with Jenkins
A simple hardware test platform would need to be constructed and connected to the jenkins server as i understand it.

* [Callet91/DEMO_Jenkins_PlatformIO](https://github.com/Callet91/DEMO_Jenkins_PlatformIO) online github repository with step by step guide on how to setup platformIO and jenkins

### Offline local PlatformIO software tests
PlatformIO developed code could be tested offline on a local host computer connected to the micro-controller.

* [Unit Testing of a “Blink” Project](https://docs.platformio.org/en/latest/tutorials/core/unit_testing_blink.html) - Needs to be connected to hardware card?
* [Unit Testing](https://docs.platformio.org/en/stable/advanced/unit-testing/index.html) PlatformIO official guide

## Component Communication

The image below illustrate how a speed sensor sends data to `High_Level_Control_Computer` and further to development PC.

communication overview

The diagram below shows different types of communication channels and IP address for different components.

```
             ┌───────────────────────────────────────────────┐
             │                  Laptop                       │
             │           High_Level_Control_Computer         │
             └────────────────────────┬──────────────────────┘
                                      │ 192.168.0.154
             ROS (Ethernet Network)   │
                                      │                       ┌───────────────────┐
                                ┌─────┴─────┐                 │                   │
                                │  Router   ├────────────────►│   Wifi Internet   │
                                └─────┬─────┘                 │                   │
                                      │ 192.168.0.1           └───────────────────┘
             ROS (Ethernet Network)   │
                                      │ 192.168.150.110
             ┌────────────────────────┴──────────────────────┐
             │      Hardware_interface_Low_Level_Computer    │
             │              Raspberry PI 4                   │
             └───────────────────────┬───────────────────────┘
                                     │ GPIO
                             ┌───────┴────────┐
                             │ RS485 CAN HAT  │
                           ┌─┤                ├─┐
                           │ │     MCP2515    │ │
                           │ └────────────────┘ │
     CAN network           │                    │
              ┌────────────┴───┐          ┌─────┴──────────┐
              │     MCP2515    │          │     MCP2515    │
              └────────┬───────┘          └───────┬────────┘
┌──────────────────────┴──────────┐    ┌──────────┴──────────────────────┐
│          STM32 Blue Pill        │    │         STM32 Blue Pill         │
│       Propulsion/Steering       │    │          Speed sensor           │
└─────────────────────────────────┘    └─────────────────────────────────┘
```
Illustration done using asciiflow online editor. (If any future changes has to be done)

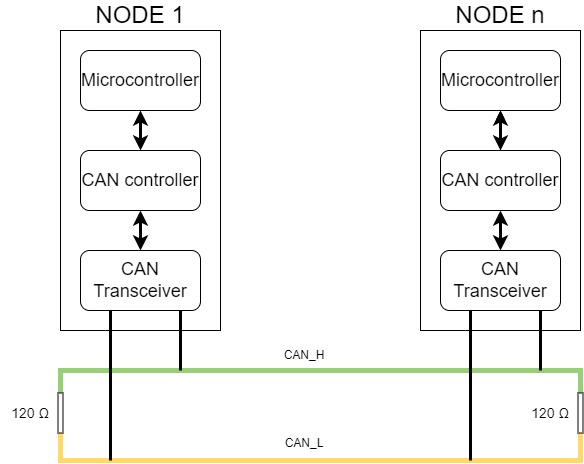
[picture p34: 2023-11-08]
Images/Report_sketches/Communication/CAN_nodes.jpg

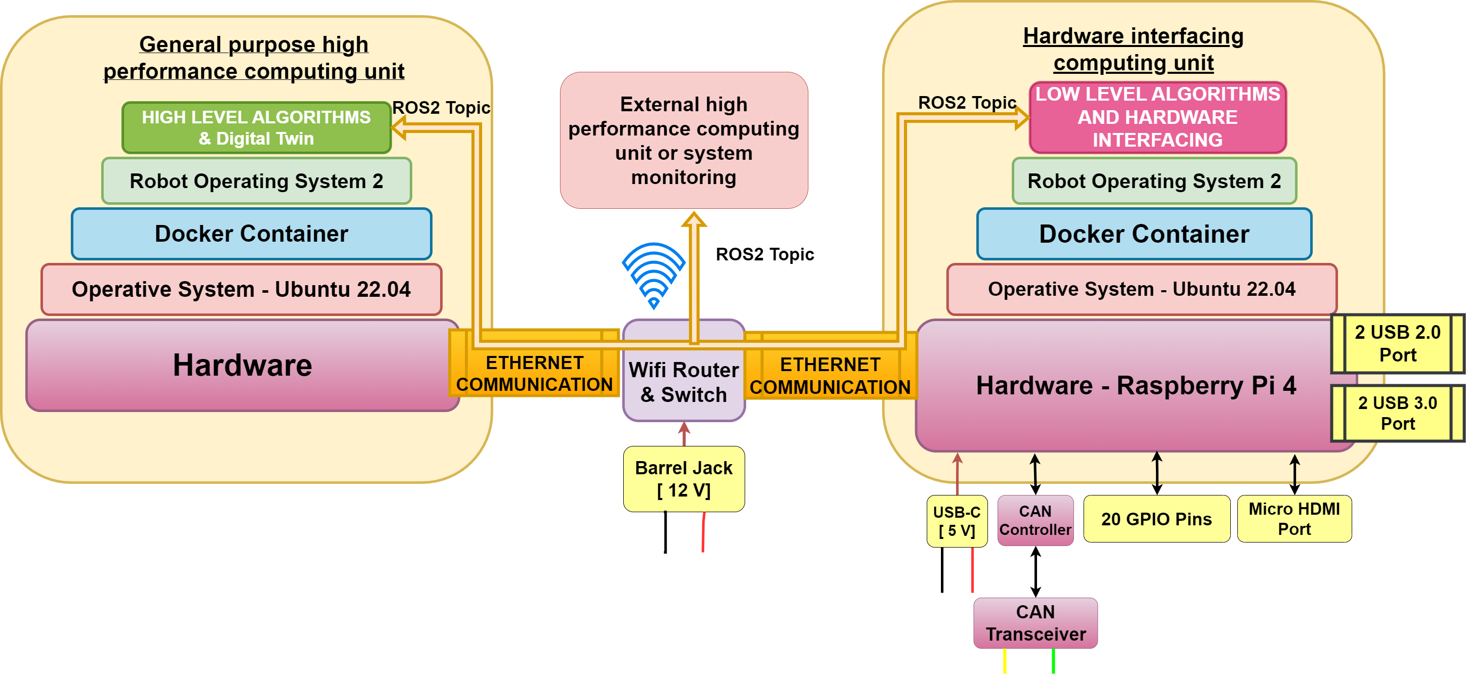
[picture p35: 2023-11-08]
Images/Report_sketches/HW/Central_master_computer.png

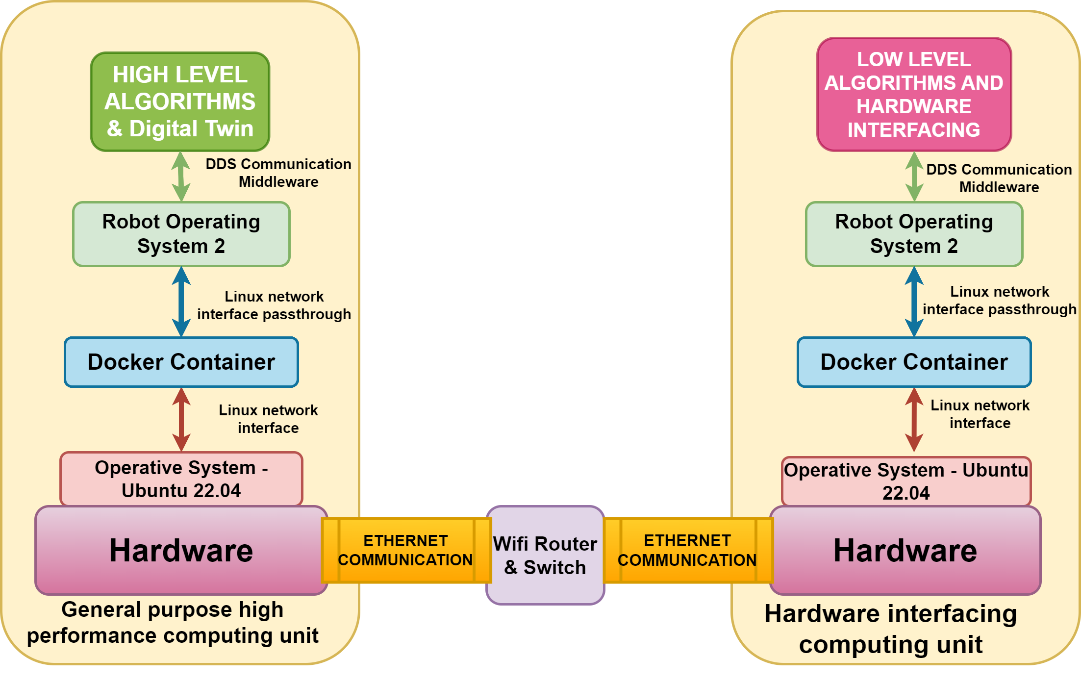
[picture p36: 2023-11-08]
Images/Report_sketches/SW/ethernet_sw_com.png

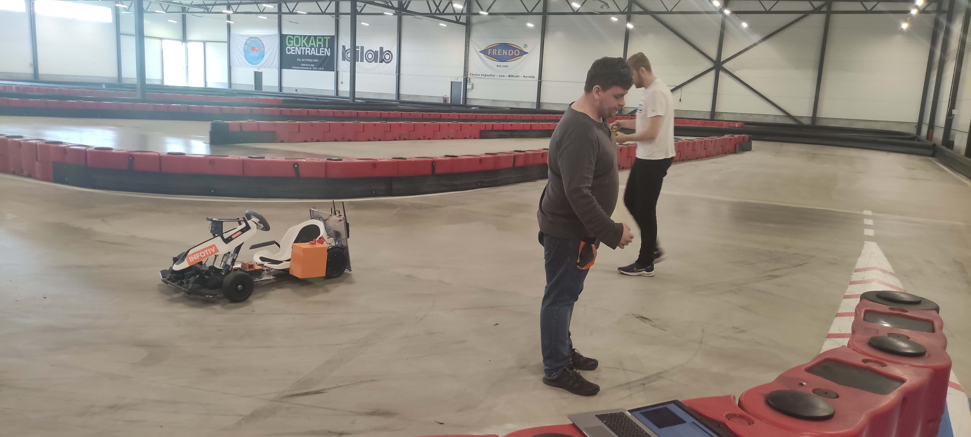
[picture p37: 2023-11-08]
Images/Pictures/TestDAY/overview.jpg

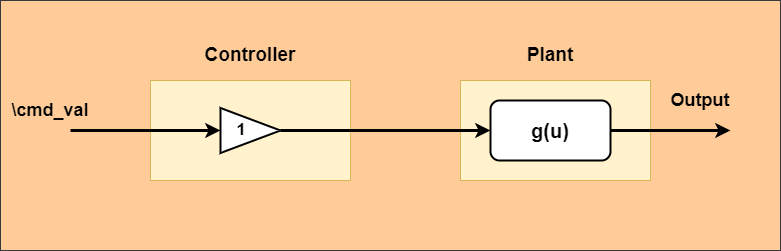
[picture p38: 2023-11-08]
Images/Report_sketches/general_controller.png

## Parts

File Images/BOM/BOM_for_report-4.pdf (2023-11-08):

# BOM Autonomous Platform Generation 4

TOTAL PRICE SEK: | 16139,3
Part Name | Quantity | Area of Use | Price (SEK)

# Sensors

USB kamera, Logitech c920 | 1

Front facing camera AP4.Documented to work well
with existing ros2 camera packages! | 1260

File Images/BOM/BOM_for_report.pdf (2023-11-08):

# BOM Autonomous Platform Generation 4

## TOTAL PRICE SEK: 16139,3

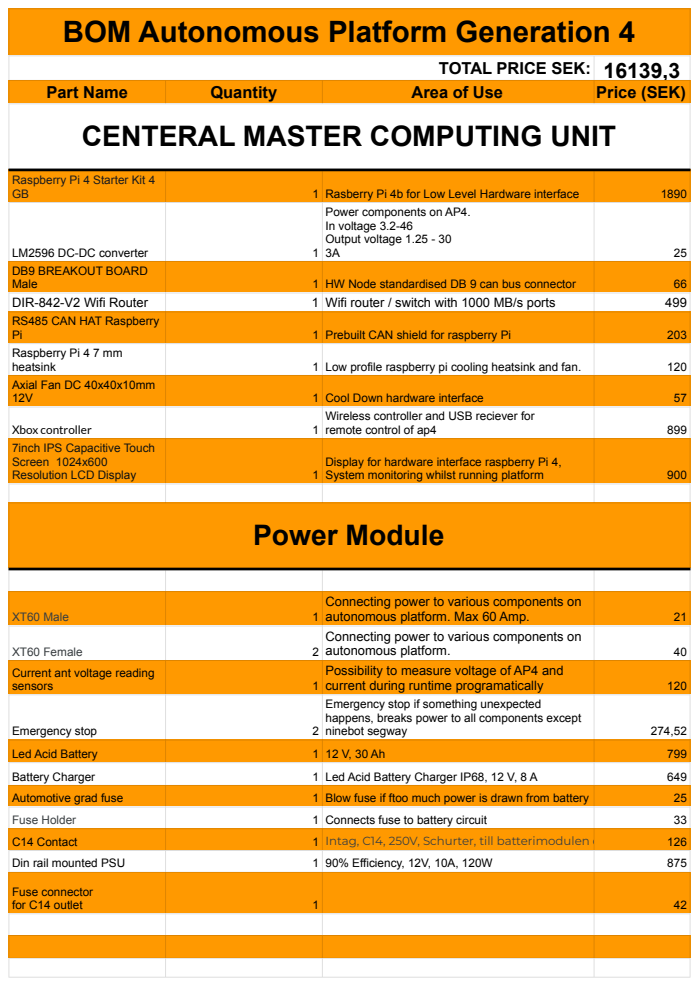
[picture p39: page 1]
Part Name; Quantity; Area of Use; Price (SEK); 1 Rasberry Pi 4b for Low Level Hardware interface; LM2596 DC-DC converter; Male; 1 HW Node standardised DB 9 can bus connector; DIR-842-V2 Wifi Router; 1 Wifi router / switch with 1000 MB/s ports; 1 Prebuilt CAN shield for raspberry Pi; heatsink; 1 Low profile raspberry pi cooling heatsink and fan.; 1 Cool Down hardware interface; Xbox controller; remote control of ap4; Resolution LCD Display; System monitoring whilst running platform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

CENTERAL MASTER COMPUTING UNIT

Raspberry Pi 4 Starter Kit 4

Power components on AP4.
In voltage 3.2-46
Output voltage 1.25 - 30

DB9 BREAKOUT BOARD
RS485 CAN HAT Raspberry
Raspberry Pi 4 7 mm
Axial Fan DC 40x40x10mm

Wireless controller and USB reciever for

7inch IPS Capacitive Touch
Screen 1024x600

Display for hardware interface raspberry Pi 4,

Connecting power to various components on
Possibility to measure voltage of AP4 and
Emergency stop if something unexpected
happens, breaks power to all components except

Current ant voltage reading

# BOM Autonomous Platform Generation 4

TOTAL PRICE SEK: | 16139,3

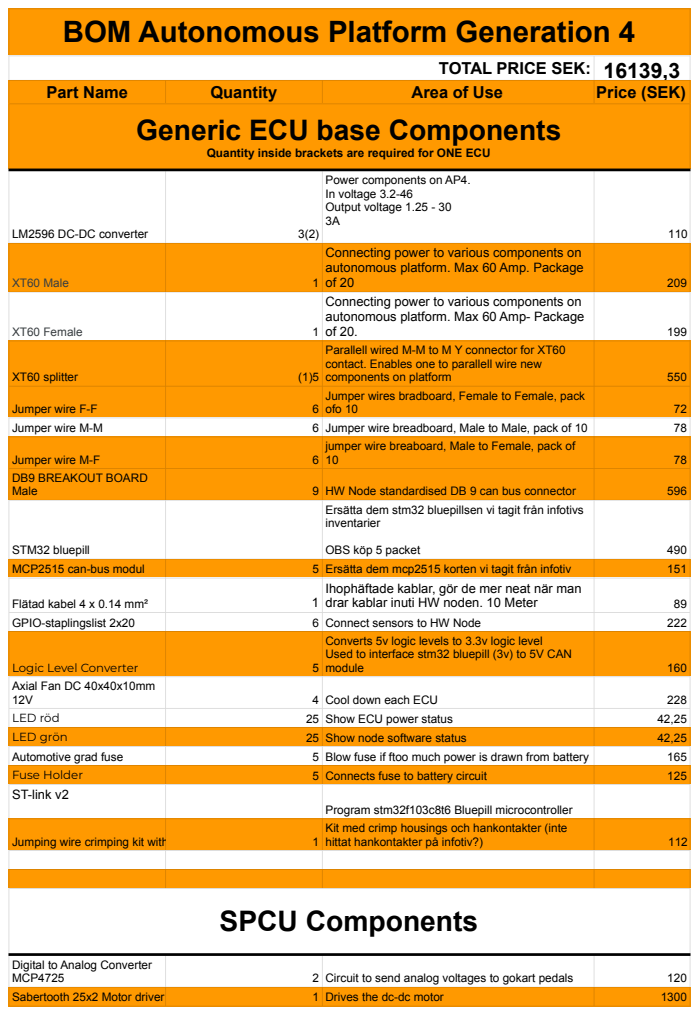
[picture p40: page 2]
LM2596 DC-DC converter; XT60 Male; XT60 Female; XT60 splitter; components on platform; Jumper wire F-F; ofo 10; Jumper wire M-M; 6 Jumper wire breadboard, Male to Male, pack of 10; Jumper wire M-F; DB9 BREAKOUT BOARD; Male; 9 HW Node standardised DB 9 can bus connector; STM32 bluepill; OBS köp 5 packet; MCP2515 can-bus modul; 5 Ersätta dem mcp2515 korten vi tagit från infotiv; Flätad kabel 4 x 0.14 mm²; drar kablar inuti HW noden. 10 Meter; GPIO-staplingslist 2x20; 6 Connect sensors to HW Node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

Part Name | Quantity | Area of Use | Price (SEK)

Generic ECU base Components

Quantity inside brackets are required for ONE ECU

Power components on AP4.
In voltage 3.2-46
Output voltage 1.25 - 30

Connecting power to various components on
autonomous platform. Max 60 Amp. Package
autonomous platform. Max 60 Amp- Package
Parallell wired M-M to M Y connector for XT60
contact. Enables one to parallell wire new
Jumper wires bradboard, Female to Female, pack

jumper wire breaboard, Male to Female, pack of

Ersätta dem stm32 bluepillsen vi tagit från infotivs
inventarier

Ihophäftade kablar, gör de mer neat när man

Converts 5v logic levels to 3.3v logic level
Used to interface stm32 bluepill (3v) to 5V CAN

Axial Fan DC 40x40x10mm

Program stm32f103c8t6 Bluepill microcontroller
Kit med crimp housings och hankontakter (inte

Digital to Analog Converter

# BOM Autonomous Platform Generation 4

TOTAL PRICE SEK: | 16139,3

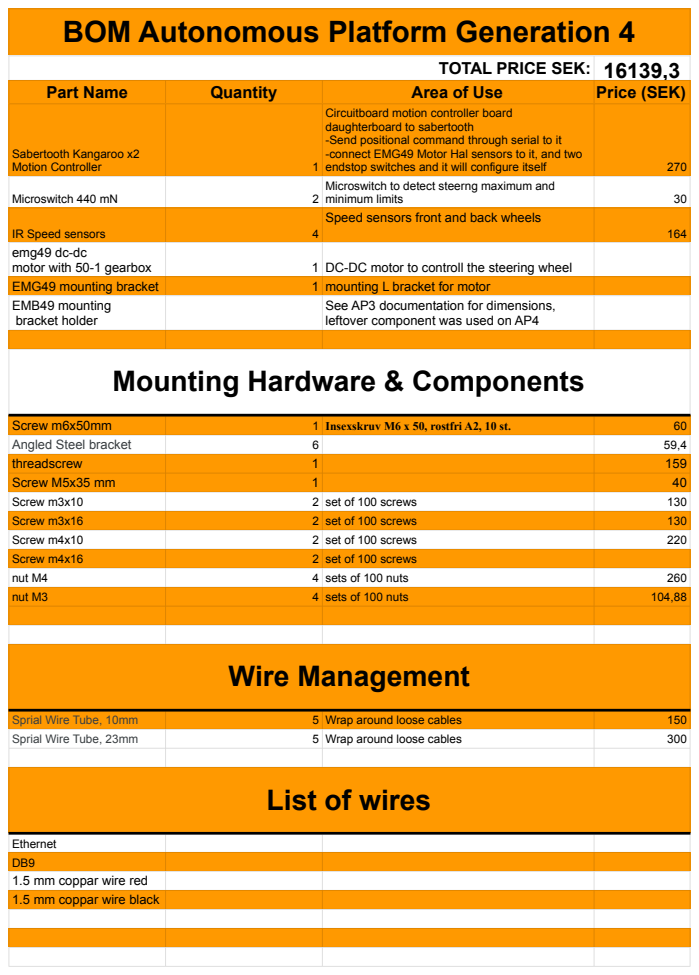
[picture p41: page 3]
Sabertooth Kangaroo x2; Motion Controller; endstop switches and it will configure itself; Microswitch 440 mN; minimum limits; IR Speed sensors; emg49 dc-dc; motor with 50-1 gearbox; 1 DC-DC motor to controll the steering wheel; EMG49 mounting bracket; 1 mounting L bracket for motor; EMB49 mounting bracket holder; Screw m6x50mm; 1 Insexskruv M6 x 50, rostfri A2, 10 st.; Angled Steel bracket; threadscrew; Screw M5x35 mm; Screw m3x10; 2 set of 100 screws; Screw m3x16; Screw m4x10; Screw m4x16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

Part Name | Quantity | Area of Use | Price (SEK)

Circuitboard motion controller board
daughterboard to sabertooth
-Send positional command through serial to it
-connect EMG49 Motor Hal sensors to it, and two
Microswitch to detect steerng maximum and
Speed sensors front and back wheels

See AP3 documentation for dimensions,
leftover component was used on AP4

Mounting Hardware & Components

List of wires

Ethernet
1.5 mm coppar wire red
1.5 mm coppar wire black

# BOM Autonomous Platform Generation 4

TOTAL PRICE SEK: | 16139,3
Part Name | Quantity | Area of Use | Price (SEK)

# Sensors

USB kamera, Logitech c920 | 1

Front facing camera AP4.Documented to work well
with existing ros2 camera packages! | 1260

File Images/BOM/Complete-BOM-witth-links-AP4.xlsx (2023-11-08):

AP4 Bill Of Materials Updated: 3/5-2023
Sum: |  |  |  |  |  |  | 16248.3 | Sum: | 922
Name | Quantity | Area of Use | Supplier | Article nr | Article nr Supplier | Link | Price (SEK) | Documentation | Aprroximate price if bought
Hardware Interface:
Purchace session 1
Digital to Analog Converter | 2 | In order to send pure Analog signals to power the motors ORDER 2 | Elfa | 935 | 300-91-226 | https://www.elfa.se/sv/mcp4725-delningskort-adafruit-935/p/30091226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 | 120
Sabertooth Motor Driver | 1 | Drive steering motor | RobotShop |  | 41002960 | https://eu.robotshop.com/products/dimension-engineering-sabertooth-2x25?variant=42600729084072 | 1300 |  |  | Sabertooth 2x25 manual https://www.dimensionengineering.com/datasheets/Sabertooth2x25.pdf Sabertooth example code https://www.dimensionengineering.com/software/SabertoothArduinoLibrary/html/ Sabertooht arduino library https://www.dimensionengineering.com/info/arduino todo hur läser vi av styrvinkeln genom serial?
Sabertooth Kangaroo x2 Motion Controller | 1 | Circuitboard motion controller board daughterboard to sabertooth -Send positional command through serial to it -connect EMG49 Motor Hal sensors to it, and two endstop switches and it will configure itself | RobotShop |  |  | https://eu.robotshop.com/products/self-tuning-kangaroo-x2-motion-controller?variant=42601684467880 | 270 |  |  | Kangaroo x2 Daughter board to sabertooth - Manual - https://www.dimensionengineering.com/datasheets/KangarooManual.pdf Någon youtube tjomme som leker runt med sabertooth kort https://www.youtube.com/watch?v=siufT2AsIZ4
Mikrobrytare 440 mN | 2 | 2 st mikrobrytare för att känna av maxlägen i styrningen | Elfa | RND 210-00755 | 302-87-010 | https://www.elfa.se/sv/mikrobrytare-3a-1co-440mn-rullarm-med-led-rnd-components-rnd-210-00755/p/30287010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 | 30
Justerbar Omvandlare ( in 3.2 - 46V) ut (1.25 - 30v) Upp till 3A | 5 | To power different component | Amazon |  |  | https://www.amazon.se/gp/product/B07DP3JX2X/ref=ppx_yo_dt_b_asin_title_o00_s00?ie=UTF8&psc=1 | 110
DIR-842-V2 | 1 | Wifi router / switch with 1000 MB/s ports | Kjell o Company |  | 61198 | https://www.kjell.com/no/produkter/nettverk/tradlose-rutere/d-link-dir-842-tradlos-ruter-ac1200-p61198 | 499
Purchace session 2
Utbyggnadsmodul SEN-Speed | 4 | Speed sensors front and back wheels | Conrad |  | 1573543 | https://www.conrad.se/p/utbyggnadsmodul-sen-speed-arduino-banana-pi-cubieboard-raspberry-pi-pcduino-1646891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 | 164
XT60 Male | 1 | Connecting power to various components on autonomous platform. Max 60 Amp. Package of 20 | conrad | 1399717 | 1399717 | https://www.conrad.se/p/reely-1399717-batterikontakt-xt60-foergylld-20-st-1399717 | 209
XT60 Female | 1 | Connecting power to various components on autonomous platform. Max 60 Amp- Package of 20. | conrad | 1399713 | 1399713 | https://www.conrad.se/p/reely-1399713-batterisockel-xt60-foergylld-20-st-1399713 | 199
Flätad kabel 4 x 0.14 mm² | 1 | Ihophäftade kablar, gör de mer neat när man drar kablar inuti HW noden. 10 Meter | conrad | 4014991244059 | 1398078 | https://www.conrad.se/p/418-5-flaetad-kabel-4-x-014-mm-groen-roed-gul-bla-5-m-1398078 | 89
Ström och Spänningsmoduler | 1 | mäta ström och spänning på batteriet | Amazon | YY-SensorModule-003 | B09F6CT827 | https://www.amazon.se/Aktuell-sensoromr%C3%A5de-Sp%C3%A4nningssensor-Sormodule-Sp%C3%A4nningsterminal/dp/B09F6CT827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 | 120
XT60 splitter | 5 | Adapterkontakt [2x XT60 - 1x XT60] parallellt ansluten Reely | Conrad | 4053199481521 | 1373227 | https://www.conrad.se/p/adapterkontakt-2x-xt60-1x-xt60-parallellt-ansluten-reely-1373227 | 275
Ninebot Go-kart 3d model | 1 | 3d model of gokart to use in digital twin illustration and to cad upp solution concepts. STL/OBJ model file types. Can import into CAD software |  |  |  | https://sketchfab.com/3d-models/ninebot-go-kart-b2ab6e2fbdcc44309585336423681e06 alternative source https://www.renderhub.com/industryofautomobile/ninebot-go-kart | 210
Purchace session 3
GPIO-staplingslist 2x20 | 6 | Connect sensors to HW Node | elfa | 2223 | 301-33-58 | https://www.elfa.se/sv/gpio-staplingslist-till-pi-pi2-pi3-2x20-adafruit-2223/p/30133581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 | 222
Dubbelriktad omvandlare av logisk spänningsnivå | 5 | Converts 5v logic levels to 3.3v logic level Used to interface stm32 bluepill (3v) to 5V CAN module | elfa | BOB-12009 | 301-45-425 | https://www.elfa.se/sv/dubbelriktad-omvandlare-av-logisk-spaenningsniva-sparkfun-electronics-bob-12009/p/30145425 | 160
Axialfläkt DC 40x40x10mm 12V | 5 | Cool down each node | elfa | EE40101S1-1000U-999 | 301-29-654 | https://www.elfa.se/sv/axialflaekt-dc-40x40x10mm-12v-13-9m-sunon-ee40101s1-1000u-999/p/30129654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 | 285
Nödstoppsbrytare | 2 | Emergency stop if something happens, breaks power to steering and autonomous drive sensors | elfa | YW1B-V4E01R | 301-02-672 | https://www.elfa.se/sv/noedstoppsbrytare-1nc-ip20-kopplingsbox-ip65-frontpanelen-idec-yw1b-v4e01r/p/30102672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 | 274.52
LED röd | 25 | for node power on (25 minsta order) | elfa | L-7113LID | 175-01-464 | https://www.elfa.se/sv/led-627nm-roed-mm-kingbright-7113lid/p/17501464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 | 42.25
LED grön | 25 | for node ok check light (25 minsta order) | elfa | L-7113LGD | 175-10-192 | https://www.elfa.se/sv/led-565nm-groen-mm-kingbright-7113lgd/p/17510192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 | 42.25
RS485 CAN HAT Raspberry Pi | 1 | Prebuilt CAN shield for raspberry Pi, avoids us hacking together a solution. SPI communication (same as MCP2515) | Amazon |  | AMAZON | https://www.amazon.se/CAN-kontroll-SPI-gr%C3%A4nssnitt-s%C3%A4ndtagare-SN65HVD230-l%C3%A5ngdistanskommunikation/dp/B09JKJCMHN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 | 203
Raspberry Pi 4 7 mm inbäddad kylfläns OBS P165-A varianten | 1 | Low profile raspberry pi cooler. The Raspberry Pi Node will use an external 40mm fan. According to the product page this cooler will allow for expansion boards (shields) to be mounted aswell | Amazon |  | P165-A | https://www.amazon.se/Geekworm-Raspberry-inb%C3%A4ddad-expansionsbr%C3%A4da-POE-f%C3%B6rl%C3%A4ngning/dp/B089CK12C6 | 120 | WIki sida kylfläns https://wiki.geekworm.com/P165
Digital to Analog Converter MCP4725 | 1 | By an additional unit. | elfa | 935 | 300-91-226 | https://www.elfa.se/sv/mcp4725-delningskort-adafruit-935/p/30091226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 | 60
Purchace session @ Biltema
Batteri | 1 | Fritidsbatteri, 12 V, 30 Ah | Biltema |  | 80-2302 | https://www.biltema.se/bil---mc/fordonsbatterier/fritidsbatterier/fritidsbatteri-12-v-30-ah-2000045930 | 799
Flatstiftsäkrings-kabel | 6 | Säkringshållare, mini med kabel | Biltema |  | 35-647 | https://www.biltema.se/bil---mc/elsystem/sakringar/sakringshallare-mini-2000016466 | 198
M6 skruv 50mm | 1 | Insexskruv M6 x 50, rostfri A2, 10 st. | Biltema |  | 89-315 | https://www.biltema.se/bygg/fastelement/maskinskruvar/insexskruv-rostfri-a2-2000017858 | 60
Flatstiftsäkringar | 6 | Flatstiftssäkring Mini, 10 st. | Biltema |  | 35-655 | https://www.biltema.se/bil---mc/elsystem/flatstiftssakringar/flatstiftssakring-mini-10-st-2000016468 | 150
laddare batteri | 1 | Batteriladdare IP68, 12 V, 8 A | Biltema |  | 37-758 | https://www.biltema.se/bil---mc/fordonsbatterier/batteriladdare/batteriladdare-ip68-12-v-8-a-2000037612 | 649
vinkeljärn | 6 | fäste på plåt | Biltema |  | 19-4884 | biltema.se/bygg/byggbeslag/vinkelbeslag/vinkelbeslag-2000017273 | 59.4
Låsskruvar | 1 | För att låsa fast kugghjul på styrmotorn | Biltema |  | 19-1080 | https://www.biltema.se/bil---mc/verkstadsutrustning/fastelement/sortimentsatser/lasskruvsats-150-delar-2000033233 | 159
Purchace session @ Clas Ohlsson
Skruv M5x35 mm | 1 |  | Class Ohlsson |  |  |  | 40
Taken from Infotivs Inventory
emg49 dc-dc motor with 50-1 gearbox | 1 | DC-DC motor to controll the steering wheel | Robot Electronics |  |  | https://www.robot-electronics.co.uk/products/emg49-gearmotor-with-encoder.html |  | https://www.robot-electronics.co.uk/htm/emg49.htm | 872
EMG49 mounting bracket | 1 | mounting L bracket for motor | Robot Electronics |  |  | https://www.robot-electronics.co.uk/emg49-mounting-bracket.html |  |  | 50
EMB49 mounting bracket holder |  | See AP3 documentation for dimensions, leftover component was used on AP4
STM32 bluepill
MCP2515 CAN controller / reciever
DC-DC converters
ST-link v2 Bluepill microcontroller flasher
Buy in middle of may
Skruv m3x10 Sexkant | 2 | set of 100 screws | Elfa | BN 610 M3X10MM | 300-71-964 (https://www.elfa.se/sv/skruv-uttagskapa-sexkant-mm-m3-10mm-paket-med-100-delar-bossard-bn-610-m3x10mm/p/30071964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) | https://www.elfa.se/sv/skruv-uttagskapa-sexkant-mm-m3-10mm-paket-med-100-delar-bossard-bn-610-m3x10mm/p/30071964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 | 130
skruv m3x16 Sexkant | 2 | set of 100 screws | Elfa | BN 610 M3X16MM | 300-71-966 (https://www.elfa.se/sv/skruv-uttagskapa-sexkant-mm-m3-16mm-paket-med-100-delar-bossard-bn-610-m3x16mm/p/30071966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) | https://www.elfa.se/sv/skruv-uttagskapa-sexkant-mm-m3-16mm-paket-med-100-delar-bossard-bn-610-m3x16mm/p/30071966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 | 130
skruv m4x10 | 2 | set of 100 screws | Elfa | BN 610 M4X10MM | 300-71-970 (https://www.elfa.se/sv/skruv-uttagskapa-sexkant-mm-m4-10mm-paket-med-100-delar-bossard-bn-610-m4x10mm/p/30071970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) | https://www.elfa.se/sv/skruv-uttagskapa-sexkant-mm-m4-10mm-paket-med-100-delar-bossard-bn-610-m4x10mm/p/30071970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 | 220
skruv m4x16 | 2 | set of 100 screws | Elfa | MC6S M4X16H | 300-72-060 (https://www.elfa.se/sv/skruv-uttagskapa-sexkant-mm-m4-16mm-paket-med-100-delar-bossard-mc6s-m4x16h/p/30072060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) | https://www.elfa.se/sv/skruv-uttagskapa-sexkant-mm-m4-16mm-paket-med-100-delar-bossard-mc6s-m4x16h/p/30072060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
Mutter M4 | 4 | sets of 100 mutter | Elfa | BN 117 M4 100 | 300-72-047 (https://www.elfa.se/sv/sexkantsmutter-m4-m4-2mm-foerzinkat-stal-bossard-bn-117-m4-100/p/30072047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) | https://www.elfa.se/sv/sexkantsmutter-m4-m4-2mm-foerzinkat-stal-bossard-bn-117-m4-100/p/30072047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 | 260
Mutter M3 | 4 | sets of 100 mutter | Elfa | 1874659 | 148-00-070 (https://www.elfa.se/sv/hex-nut-m3-m3-4mm-foerzinkat-stal-bossard-m6m-m3/p/14800070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) | https://www.elfa.se/sv/hex-nut-m3-m3-4mm-foerzinkat-stal-bossard-m6m-m3/p/14800070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 | 104.88
Jumper wire F-F | 6 | Jumper wires bradboard, Female to Female, pack ofo 10 | Elfa | RND 255-00011 | 301-15-109 (https://www.elfa.se/en/jumper-wire-female-to-female-pack-of-10-pieces-150-mm-multicoloured-rnd-components-rnd-255-00011/p/30115109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) | https://www.elfa.se/en/jumper-wire-female-to-female-pack-of-10-pieces-150-mm-multicoloured-rnd-components-rnd-255-00011/p/30115109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 | 72
Jumper wire M-M | 6 | Jumper wire breadboard, Male to Male, pack of 10 | Elfa | RND 255-00015 | 301-15-113 (https://www.elfa.se/en/jumper-wire-male-to-male-pack-of-10-pieces-150-mm-multicoloured-rnd-components-rnd-255-00015/p/30115113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) | https://www.elfa.se/en/jumper-wire-male-to-male-pack-of-10-pieces-150-mm-multicoloured-rnd-components-rnd-255-00015/p/30115113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 | 78
Jumper wire M-F | 6 | jumper wire breaboard, Male to Female, pack of 10 | Elfa | RND 255-00012 | 301-15-110 (https://www.elfa.se/en/jumper-wire-male-to-female-pack-of-10-pieces-150-mm-black-rnd-components-rnd-255-00012/p/30115110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) | https://www.elfa.se/en/jumper-wire-male-to-female-pack-of-10-pieces-150-mm-black-rnd-components-rnd-255-00012/p/30115110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 | 78
C14 kontakt hona | 1 | Intag, C14, 250V, Schurter, till batterimodulen och externt PSU | Elfa | DD11.0114.1111 | 169-63-555 (https://www.elfa.se/sv/intag-c14-250v-schurter-dd11-0114-1111/p/16963555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) | https://www.elfa.se/sv/intag-c14-250v-schurter-dd11-0114-1111/p/16963555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 | 126
Nätaggregat för DIN-skenemontage, 90%, 12V, 10A, 120W | 1 | Battery module PSU | Elfa | WDR-120-12 | 169-36-736 (https://www.elfa.se/sv/naetaggregat-foer-din-skenemontage-90-12v-10a-120w-justerbar-mean-well-wdr-120-12/p/16936736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) | https://www.elfa.se/sv/naetaggregat-foer-din-skenemontage-90-12v-10a-120w-justerbar-mean-well-wdr-120-12/p/16936736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 | 875
Raspberry Pi 4 Starter Kit 4 GB | 1 | Raspberry Pi till AP4, hittils har vi lånat från ML kursen | Webbhallen |  | 358177 (https://www.webhallen.com/se/product/358177-Raspberry-Pi-4-Starter-Kit-4-GB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) | https://www.webhallen.com/se/product/358177-Raspberry-Pi-4-Starter-Kit-4-GB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 | 1890
DB9 BREAKOUT BOARD SIENOC RS232 D-SUB DB9 hane till terminalkontakt signalmodul | 10 | Ersätta de terminalblock som vi tagit från infotivs inventarier | Amazon |  |  | https://www.amazon.se/SIENOC-RS232-D-SUB-terminalkontakt-signalmodul/dp/B01M8JRDN0 | 660
STM32 bluepill |  | Ersätta dem stm32 bluepillsen vi tagit från infotivs inventarier OBS köp 5 packet | Amazon |  |  | https://www.amazon.se/AZDelivery-mikrokontroller-STM32F103C8T6-utvecklingskortmodul-M3-processor/dp/B07TSKNWQQ | 490
MCP2515 can-bus modul | 5 | Ersätta dem mcp2515 korten vi tagit från infotiv | Amazon |  |  | https://www.amazon.se/ZkeeShop-CAN-bussmodul-mottagare-kompatibel-utvecklingskort/dp/B07SYH9BXS | 151
Jumping wire crimping kit with housings | 1 | Kit med crimp housings och hankontakter (inte hittat hankontakter på infotiv?) | Amazon |  |  | https://www.amazon.se/PERFETSELL-kontaktset-pinheader-experiment-g%C3%B6r-det-sj%C3%A4lv-projekt/dp/B085RPXY73 | 112
Last buy round
USB kamera, Logitech c920 | 1 | Framåtriktad kamera på AP4. Robust kamera med bra omdömen Documented to work with existing ros2 camera packages! | Elfa | 960-001055 | 301-80-891 (https://www.elfa.se/sv/webcam-c920-pro-1920-1080-30fps-78-usb-logitech-960-001055/p/30180891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) | https://www.elfa.se/sv/webcam-c920-pro-1920-1080-30fps-78-usb-logitech-960-001055/p/30180891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 | 1260 (https://software-dl.ti.com/jacinto7/esd/robotics-sdk/latest/docs/source/ros1/drivers/mono_capture/README.html)
RGB LED LIST | 1 | LED RGD list för att indikera platformens status, drivs med 5v, drar 3.6 A, längd 1 meter | Elfa | 104020109 | 301-21-594 (https://www.elfa.se/sv/ws2813-rgb-led-list-60-lysdioder-rgb-5v-6a-18w-1m-ws2813-seeed-studio-104020109/p/30121594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) | https://www.elfa.se/sv/ws2813-rgb-led-list-60-lysdioder-rgb-5v-6a-18w-1m-ws2813-seeed-studio-104020109/p/30121594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 | 132
4301.1407 - Säkringsinsats 1-pol, 5 x 20 mm,, Schurter | 1 | Borde passa denna https://www.elfa.se/sv/intag-c14-250v-schurter-dd11-0114-1111/p/16963555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 om vi tolka medföljande dokument rätt | Elfa | 180.1854167 | 169-62-956 (https://www.elfa.se/sv/saekringsinsats-pol-20-mm-schurter-4301-1407/p/16962956) | https://www.elfa.se/sv/saekringsinsats-pol-20-mm-schurter-4301-1407/p/16962956 | 42
GLAS SÄKRINGAR ???
XT60 Y SPLITTER | 5 | XT60 Y splitter to parell wire electrical componts on AP4 | Conrad | 1373227 | 1373227 (https://www.conrad.se/p/adapterkontakt-2x-xt60-1x-xt60-parallellt-ansluten-reely-1373227) | https://www.conrad.se/p/adapterkontakt-2x-xt60-1x-xt60-parallellt-ansluten-reely-1373227 | 70
Skyddsslang, 10mm | 5 | Pris per meter Skyddsslang att lindra in kablage på AP4 med | elfa | SHR-08-PPB | 155-12-009 (https://www.elfa.se/sv/skyddsslang-10mm-polypropylen-svart-1m-essentra-shr-08-ppb/p/15512009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) | https://www.elfa.se/sv/skyddsslang-10mm-polypropylen-svart-1m-essentra-shr-08-ppb/p/15512009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 | 150
Skyddsslang, 23mm | 5 | Pris per meter Skyddsslang att lindra in kablage på AP4 med | elfa | SHR-20-PPB | 155-12-025 (https://www.elfa.se/sv/skyddsslang-23mm-polypropylen-svart-1m-essentra-shr-20-ppb/p/15512025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) | https://www.elfa.se/sv/skyddsslang-23mm-polypropylen-svart-1m-essentra-shr-20-ppb/p/15512025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 | 300
Xbox Trådlös handkontroll med Wireless Adapter | 1 | Remote control of ap4 | kjell |  | 62955 (https://www.kjell.com/se/produkter/tv-spel-gaming/handkontroller/xbox-tradlos-handkontroll-med-wireless-adapter-p62955) | https://www.kjell.com/se/produkter/tv-spel-gaming/handkontroller/xbox-tradlos-handkontroll-med-wireless-adapter-p62955 | 899
7inch IPS Capacitive Touch Screen 1024x600 Resolution LCD Display | 1 | Platform raspberryi Pi monitoring Det var bökigt att behöva släpa med en extern desktop skärm vid första gokart testet. | Amazon |  |  | https://www.amazon.se/Waveshare-7inch-Capacitive-Resolution-LCD/dp/B077PLVZCX?th=1 | 900

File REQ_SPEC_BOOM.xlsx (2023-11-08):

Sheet: System Requirement
Requirement nr | Function | Minimum requirements | Desireble requirements | Minimum specification | Desireble specification | Priority for this thesis [Low:0 ; High:10] | Verification Method | Choosen solution | Weight Criteria [ chosen vs alternative solution ] | Alternative implementation
1 | BMS and Power Management System | Shall have: - Switch between battery and PSU - Supply 12 V - Enough energy storage capacity to operate for longer periods | Inclusive the minimum requirement, it shall also have: - Internal fuses to protect battery and circuits on the platform - Measure voltage and amperage - Simple user inerface and be easily operated - Killswitch - function to check SoC | Shall meet: -Supplies 12 V +-0.5 V to system continously - voltage does not drop more than 0.5 V during load - Autonomous platform should be able to run for one hour continously without being connected to a wall outlet | Including minimum specification shall also meet: - 10 A of current continously for 1 hour - 20 A of current during peaks < 5 seconds | 10 | Minimum - Measure the voltages in each output using multimeter - Timing of test run Desireble: - For switches/Charging measure the current and voltage so that it behaves expected. i.e when current should flow or not in each circuit | Led Acid battery, Car battery charger, PSU , 12v regulator and several Voltage converters (5.5 ; 3.3 V) | Simplicity vs Cost, Led-Acid could be safer | LiPO batteries, custom built battery pack and wall connected PSU
2 | Steering control | Shall have: - Set steering angles for max left and right | Inclusive the minimum requirement, it shall also have: - easy calibration method for steering angles - measuring the angle - set steering accurate according to a given angle | Shall meet: - Possibility to manually calibrate steering angles - within a 20% margin meet a given steering angle | Inclusive the minimum specification, it shall also meet: - Calibration at start up - measure the angle within a 10% margin | 10 | - Manually measure with a protractor - Optically see how the steering limits changes after manual calibration - Optically see how the calibration algroritms returns the limits | Re-use the current solution and backengineer how they made it | Efficiency, simplicity and cost good enough solution as it is | Build a custom steering unit, using a large Nema 23 stepper motor, encoder, stepper motor driver. Re engineer mechanical parts for steering
3 | Propulsion control | Shall have: - From a command drive forward, accelerate, brake - Possibility to activate reverse mode - Simple Proportional Controller | Inclusive the minimum requirement, it shall also have: - Fast Feedback controller with a speed sensor | Shall meet: - In reversemode, internal gokart system detects and starts beeping - When throttle is increased the relative velocity is positive - When braking is increased the relative velocity goes to 0 - At full brake, the braking distance should be lower than 6m - The delay between the HWI communication and the go-kart segway shall be less than 100 ms. | Inclusive the minimum specification, it should also meet: - time constant of less than 1 sec - error of maximum 10% after 3 sec | 10 | Minimum: - Optically see how the gokart moves according to commands given - manually measure the braking distance - time the proportional controller Desireble: - perform a test run with unit step input - Measure and log the speed with time stamps - Log reference values with time stamps - Compare, visualize and calculate the key values | Analog signals from a microcontroller to send signals to the motor with feedback of speed sensors | Effiency, time and simplicity good enough | Reverse engineer the communication protocoll between the gokart module and the segway to read current velocity and send velocity commands
4 | Computing unit | Shall have: - Capability to run a operating system - Capability to run highlevel programs such as python - GPIO pins - USB port - Enough memory - Ethernet - Possibility to connect monitor, keyboards and mouse | Inclusive the minimum requirement, it should also have: - Possibility to replace and uppgrade computer HW | Shall meet: - requirement list for running ubuntu - 10 GPIO pins - 1 usb port - 1 hdmi port - 120 GB hardrive - standard ethernet port | Including minimum specification, shall also meet: - multiple usb 3.0 ports - ethernet 100 Mbit/s - 30 GPIO pins - Can run multithread | 10 | - Checking technical specification of possible computing units | Split the computing unit into two parts A Raspberry Pi 4 8gb to interface with hardware (GPIO / USB./ CAN) and run lower level algrothims to collect sensory data A heavy duty computing computer, Like an Intel Nuc or laptop to run high level algorithms | Performance | Raspberry Pi 4 for everything. Could be a potentiall bottleneck when running gazebo / digital twin simulations
5 | E/E Architecture and modularity | Shall have: - Centralized E/E architecture - Possibility to integrate new ECUs components - Follow automotive and other standards - Possibility to change the physical layout of HW | Including minimal requirements, it shall also have: - Easy integration of new ECUs - Highly scalable and modular functionalities - Intuitive Software design for easier uppgrading/replacing code | Shall meet: - one central comuting unit for highlevel control - one hardware interfacing ECU - Follows mostly the standards - Response time ECU <-> Central, less than 500 ms - ECU update frequency should not be lower than 20 Hz - while integrating new ECUs, older ones should still be compatible without needing updates (SW and HW) | Including the minimum specification, it should also meet: - ECU update frequency should not be lower than 100 Hz - Multiple ECUs integrated - Response time ECU <-> 10 ms - Guides and instructions on how to implement future functionalities | 10 | - Use timers in programs - Standards | see above
6 | Transportation Rig / Lift aid |  | It shall: - Simple to use and ease/prevent of back-pain - Fit into car with back seats folded down - Lift the gokart of the ground - Be able to pull the gokart with the rig |  | Shall meet: - The physical limits of the gokart | 2 | - Test equipment on gokart and see possible tensions/ fracture points | 3d Printed lift arrangement | time and effert, back muscles | Table with wheels
7 | Usability / Unit Tests | Shall have: - Simple startup/init procedure - Internal tests - Give user feedback when enecountered errors - Easy to modify SW |  | Shall meet: - Automatic startup when powers on - When error occured, give user information of where and why it occured. In each ECU and central computer - Documentation on how each ECUs HW/SW is constructed and how to modify |  | 5 | - Automatic scripts and prints error | Naming standard, well written documentation, having usuability in mind whilst developing | usability | no documentation, user is expected to learn by failing
8 | (SW) Digital Twin | Shall have: - Central computing units SW enables the use of a digital twin | Including the minimum requirements, it shall also have: - A accurate digital twin of the AP4 implemented -A digital twin to test high level functionalities -Simplified 3D model and visualization of AP4 and/or its sensor readings - Should be modular and scalable | Shall meet: - Use of SW development tools that can include simulation of physical dynamics and controls | Including the minimum specification, it shall also meet: - should include all sensors and actuators that is used - sensors measuring variation should not differ more than 10% from the actual HW - Digital Twin having same control highlevel algorithms | 10 | - Log data and sensor input from HW - Use sensor inputs in digital twin - Compare the differences | Gazebo | Ease of integration into ROS | CARLA, Unity, Matlab/Simulink
9 | (SW) Modular Software for Control | Shall have: - Capability to use external software tools/libraries to modify and control the AP4 |  | Shall meet: - Is the SW control designed in such a way that velocity and steering can be set without any updates on the low level SW and communication tools. - Possible to access the state of AP4 and its readings from sensors |  | 8 | - Create a very simple high level control, only affecting the mentioned high level SW | -xbox controller inputs in ROS => Remote controling of AP4 | easy to implement, easier to verify and do test cases, not under the hood technology | open pilot
10 | Safety | Shall have: - All circuits should be dimensioned accordingly to the specifications of each circuit board. Furthermore, a sufficient wire diameter shall be used according to the current flowing through. - Battery should be placed and used in a safe way by users - Battery should have a kill switch connected to emergency stop / manual switch - Go Kart shall have a designated fire extinguisher for electronics purpose - Clear schematics of current carrying cables - No open terminals |  | - | - | 10
11 | Sensors in AP4 (HW and SW) | Shall have: - Possibility to easily add new sensors - Should fit on AP4 |  | Shall meet: - A list of the most common used sensors in AD and ADAS - Meet the reasonable physical/ scale limitation of AP4 |  | 8 | - Litterature study investigation of what sensors are most commonly used in the automotive industry |  | BLOGG länk där de förklarar i layman terms vilka sensorer som är vanligast i en självkörande bil (https://www.blickfeld.com/blog/sensor-fusion-for-autonomous-driving/)
12 | Budget | Shall have: - Meet the budget requirement from Infotiv |  | Shall meet: - total cost up to 30 000 sek |  | 6 | - Budgethandling in excel

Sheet: BOOM
BOM Autonomous Platform Generation 4
TOTAL PRICE SEK: |  |  | 16139.3
Part Name | Quantity | Area of Use | Price (SEK)
CENTERAL MASTER COMPUTING UNIT
Raspberry Pi 4 Starter Kit 4 GB | 1 | Rasberry Pi 4b for Low Level Hardware interface | 1890
LM2596 DC-DC converter | 1 | Power components on AP4. In voltage 3.2-46 Output voltage 1.25 - 30 3A | 25
DB9 BREAKOUT BOARD Male | 1 | HW Node standardised DB 9 can bus connector | 66
DIR-842-V2 Wifi Router | 1 | Wifi router / switch with 1000 MB/s ports | 499
RS485 CAN HAT Raspberry Pi | 1 | Prebuilt CAN shield for raspberry Pi | 203
Raspberry Pi 4 7 mm heatsink | 1 | Low profile raspberry pi cooling heatsink and fan. | 120
Axial Fan DC 40x40x10mm 12V | 1 | Cool Down hardware interface | 57
Xbox controller | 1 | Wireless controller and USB reciever for remote control of ap4 | 899
7inch IPS Capacitive Touch Screen 1024x600 Resolution LCD Display | 1 | Display for hardware interface raspberry Pi 4, System monitoring whilst running platform | 900
Power Module
XT60 Male | 1 | Connecting power to various components on autonomous platform. Max 60 Amp. | 21
XT60 Female | 2 | Connecting power to various components on autonomous platform. | 40
Current ant voltage reading sensors | 1 | Possibility to measure voltage of AP4 and current during runtime programatically | 120
Emergency stop | 2 | Emergency stop if something unexpected happens, breaks power to all components except ninebot segway | 274.52
Led Acid Battery | 1 | 12 V, 30 Ah | 799
Battery Charger | 1 | Led Acid Battery Charger IP68, 12 V, 8 A | 649
Automotive grad fuse | 1 | Blow fuse if ftoo much power is drawn from battery | 25
Fuse Holder | 1 | Connects fuse to battery circuit | 33
C14 Contact | 1 | Intag, C14, 250V, Schurter, till batterimodulen och externt PSU | 126
Din rail mounted PSU | 1 | 90% Efficiency, 12V, 10A, 120W | 875
Fuse connector for C14 outlet | 1 |  | 42
Generic ECU base Components Quantity inside brackets are required for ONE ECU
LM2596 DC-DC converter | 3(2) | Power components on AP4. In voltage 3.2-46 Output voltage 1.25 - 30 3A | 110
XT60 Male | 1 | Connecting power to various components on autonomous platform. Max 60 Amp. Package of 20 | 209
XT60 Female | 1 | Connecting power to various components on autonomous platform. Max 60 Amp- Package of 20. | 199
XT60 splitter | (1)5 | Parallell wired M-M to M Y connector for XT60 contact. Enables one to parallell wire new components on platform | 550
Jumper wire F-F | 6 | Jumper wires bradboard, Female to Female, pack ofo 10 | 72
Jumper wire M-M | 6 | Jumper wire breadboard, Male to Male, pack of 10 | 78
Jumper wire M-F | 6 | jumper wire breaboard, Male to Female, pack of 10 | 78
DB9 BREAKOUT BOARD Male | 9 | HW Node standardised DB 9 can bus connector | 596
STM32 bluepill |  | Ersätta dem stm32 bluepillsen vi tagit från infotivs inventarier OBS köp 5 packet | 490
MCP2515 can-bus modul | 5 | Ersätta dem mcp2515 korten vi tagit från infotiv | 151
Flätad kabel 4 x 0.14 mm² | 1 | Ihophäftade kablar, gör de mer neat när man drar kablar inuti HW noden. 10 Meter | 89
GPIO-staplingslist 2x20 | 6 | Connect sensors to HW Node | 222
Logic Level Converter | 5 | Converts 5v logic levels to 3.3v logic level Used to interface stm32 bluepill (3v) to 5V CAN module | 160
Axial Fan DC 40x40x10mm 12V | 4 | Cool down each ECU | 228
LED röd | 25 | Show ECU power status | 42.25
LED grön | 25 | Show node software status | 42.25
Automotive grad fuse | 5 | Blow fuse if ftoo much power is drawn from battery | 165
Fuse Holder | 5 | Connects fuse to battery circuit | 125
ST-link v2 |  | Program stm32f103c8t6 Bluepill microcontroller
Jumping wire crimping kit with housings | 1 | Kit med crimp housings och hankontakter (inte hittat hankontakter på infotiv?) | 112
SPCU Components
Digital to Analog Converter MCP4725 | 2 | Circuit to send analog voltages to gokart pedals | 120
Sabertooth 25x2 Motor driver | 1 | Drives the dc-dc motor | 1300
Sabertooth Kangaroo x2 Motion Controller | 1 | Circuitboard motion controller board daughterboard to sabertooth -Send positional command through serial to it -connect EMG49 Motor Hal sensors to it, and two endstop switches and it will configure itself | 270
Microswitch 440 mN | 2 | Microswitch to detect steerng maximum and minimum limits | 30
IR Speed sensors | 4 | Speed sensors front and back wheels | 164
emg49 dc-dc motor with 50-1 gearbox | 1 | DC-DC motor to controll the steering wheel
EMG49 mounting bracket | 1 | mounting L bracket for motor
EMB49 mounting bracket holder |  | See AP3 documentation for dimensions, leftover component was used on AP4
Mounting Hardware & Components
Screw m6x50mm | 1 | Insexskruv M6 x 50, rostfri A2, 10 st. | 60
Angled Steel bracket | 6 |  | 59.4
threadscrew | 1 |  | 159
Screw M5x35 mm | 1 |  | 40
Screw m3x10 | 2 | set of 100 screws | 130
Screw m3x16 | 2 | set of 100 screws | 130
Screw m4x10 | 2 | set of 100 screws | 220
Screw m4x16 | 2 | set of 100 screws
nut M4 | 4 | sets of 100 nuts | 260
nut M3 | 4 | sets of 100 nuts | 104.88
Wire Management
Sprial Wire Tube, 10mm | 5 | Wrap around loose cables | 150
Sprial Wire Tube, 23mm | 5 | Wrap around loose cables | 300
List of wires
Ethernet
DB9
1.5 mm coppar wire red
1.5 mm coppar wire black
USB
Sensors
USB kamera, Logitech c920 | 1 | Front facing camera AP4.Documented to work well with existing ros2 camera packages! | 1260 (https://software-dl.ti.com/jacinto7/esd/robotics-sdk/latest/docs/source/ros1/drivers/mono_capture/README.html)

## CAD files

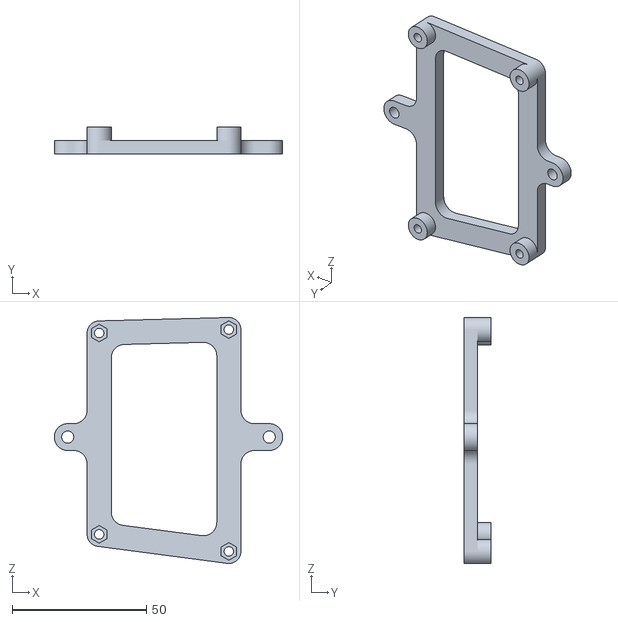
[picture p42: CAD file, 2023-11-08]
CAD/Arduino_Mega_holder/adapter.stl
85.0 x 10.0 x 91.5

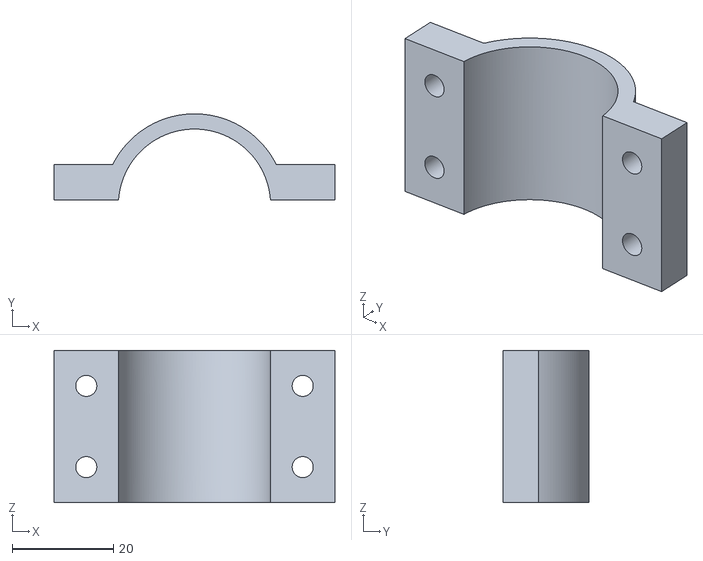
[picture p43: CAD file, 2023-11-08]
CAD/Back_plate_holder/holder_under.stl
55.4 x 17.0 x 30.0

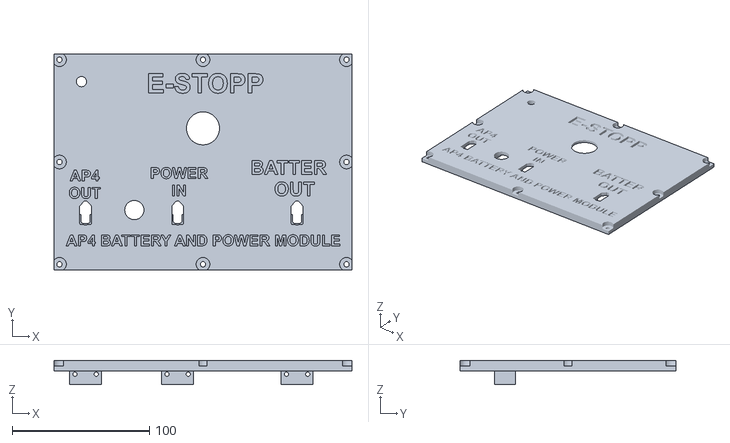
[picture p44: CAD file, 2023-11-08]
CAD/Battery_BOX/Top.stl
217.0 x 157.0 x 17.5

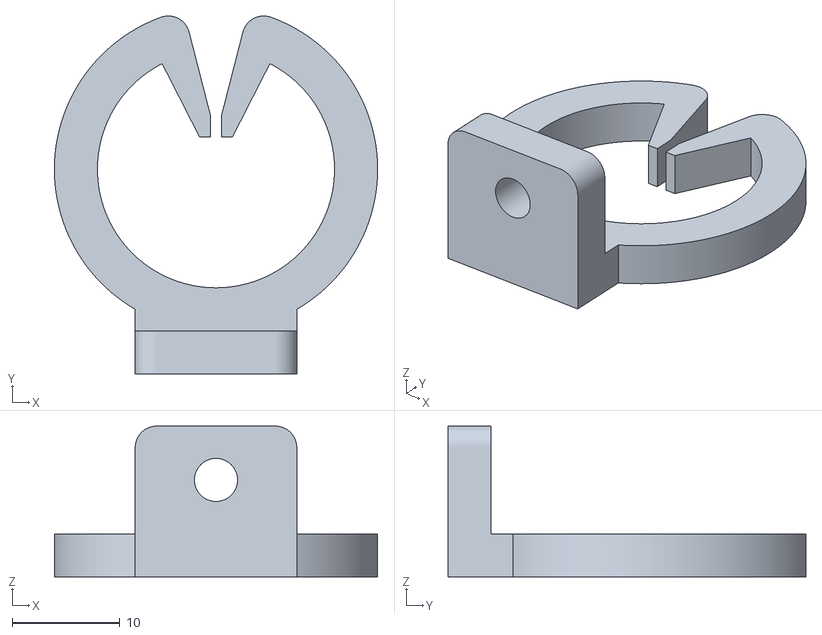
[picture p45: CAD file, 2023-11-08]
CAD/Cable_Management/files/Cable_management2.0.stl
30.0 x 33.2 x 14.0

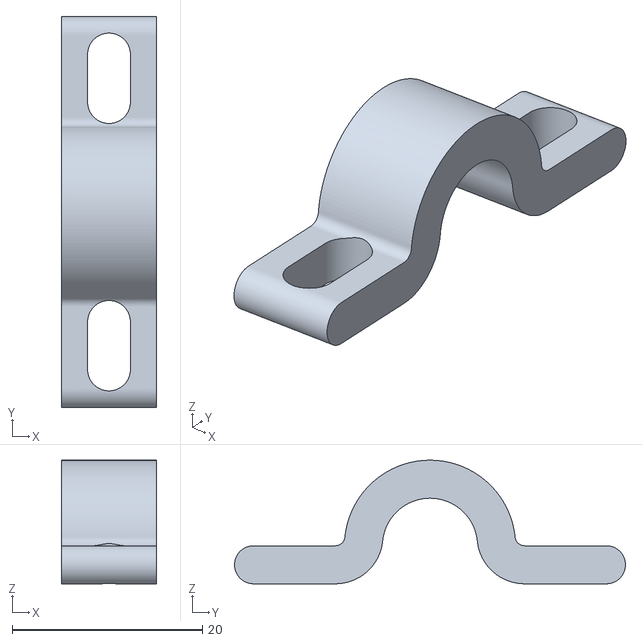
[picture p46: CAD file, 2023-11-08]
CAD/Cable_Management/small_spiral_sleve_holder.stl
10.0 x 41.1 x 13.0

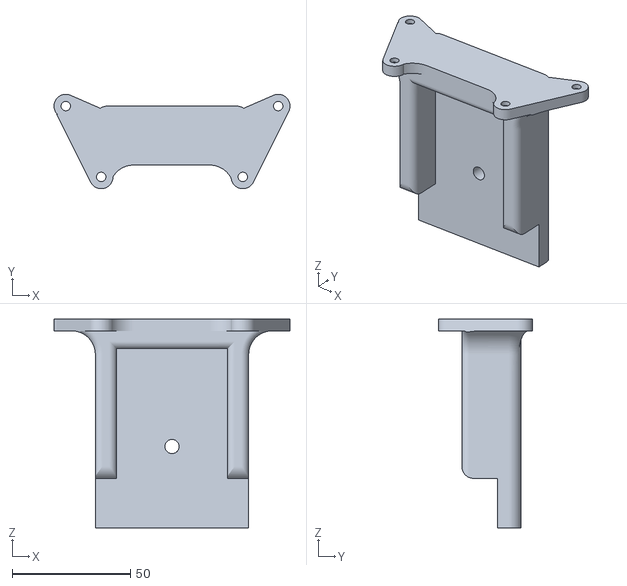
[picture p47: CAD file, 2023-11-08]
CAD/camera_sensor_mount/camera_holder.stl
100.0 x 40.0 x 88.5

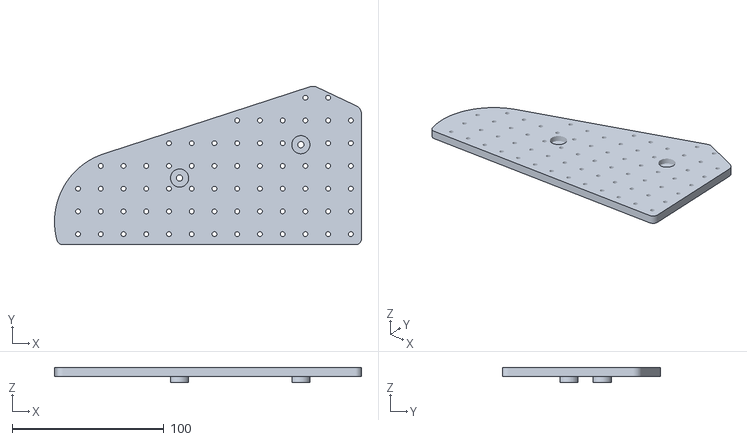
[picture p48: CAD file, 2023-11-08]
CAD/front_win_grid/front_wing_grid.stl
202.5 x 104.6 x 10.0

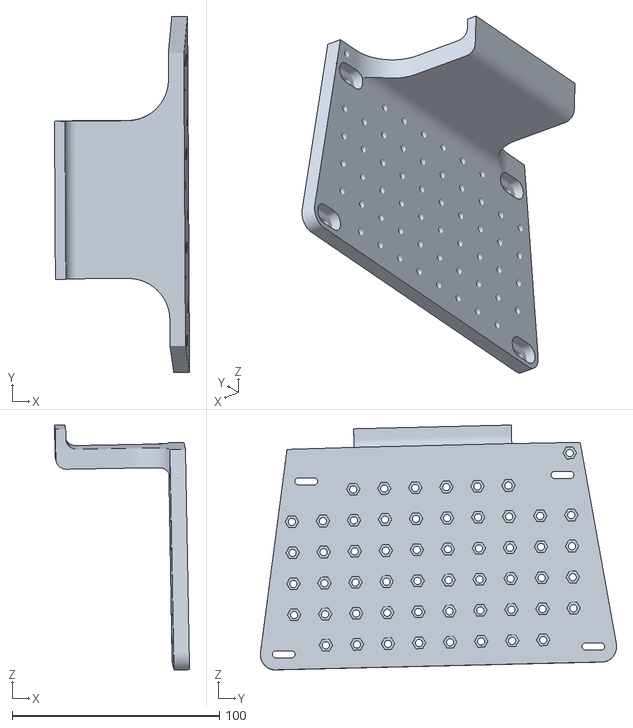
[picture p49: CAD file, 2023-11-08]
CAD/laptop_holder/laptop_holder_hole_board.stl
65.2 x 172.1 x 118.3

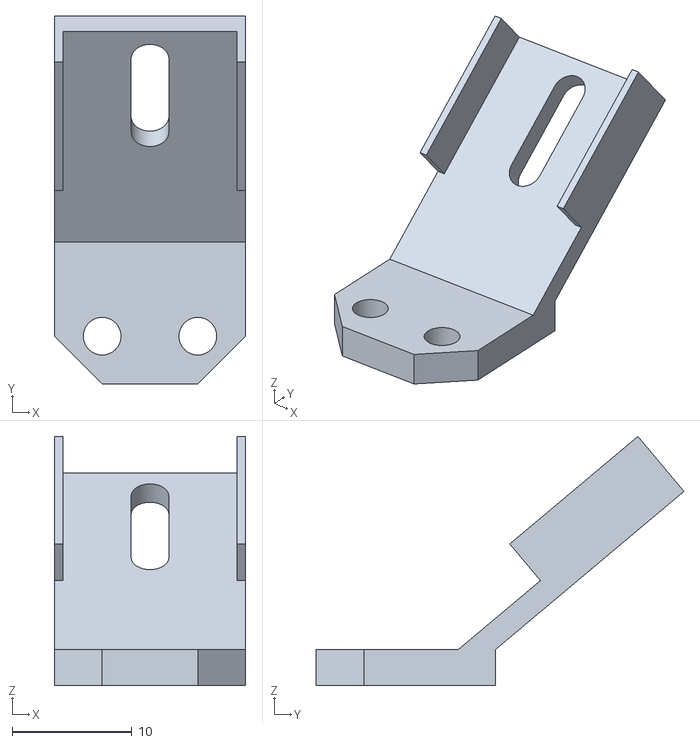
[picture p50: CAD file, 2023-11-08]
CAD/Limitswitch_steering_holder/sensor_holder.stl
16.0 x 30.8 x 20.8

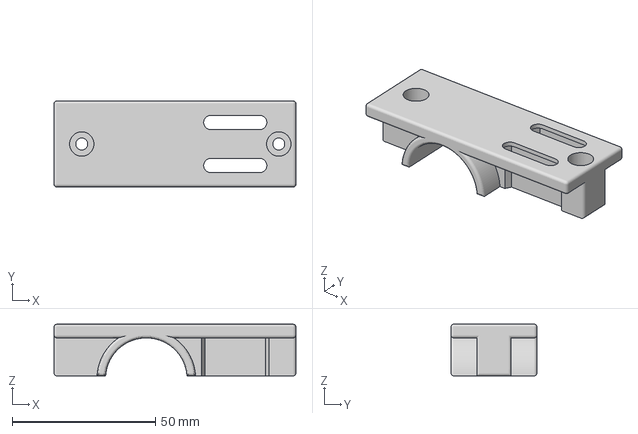
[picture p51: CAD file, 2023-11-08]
CAD/Mounting_Plate/plate_holder_top.3mf
84.3 x 30.0 x 18.0 mm

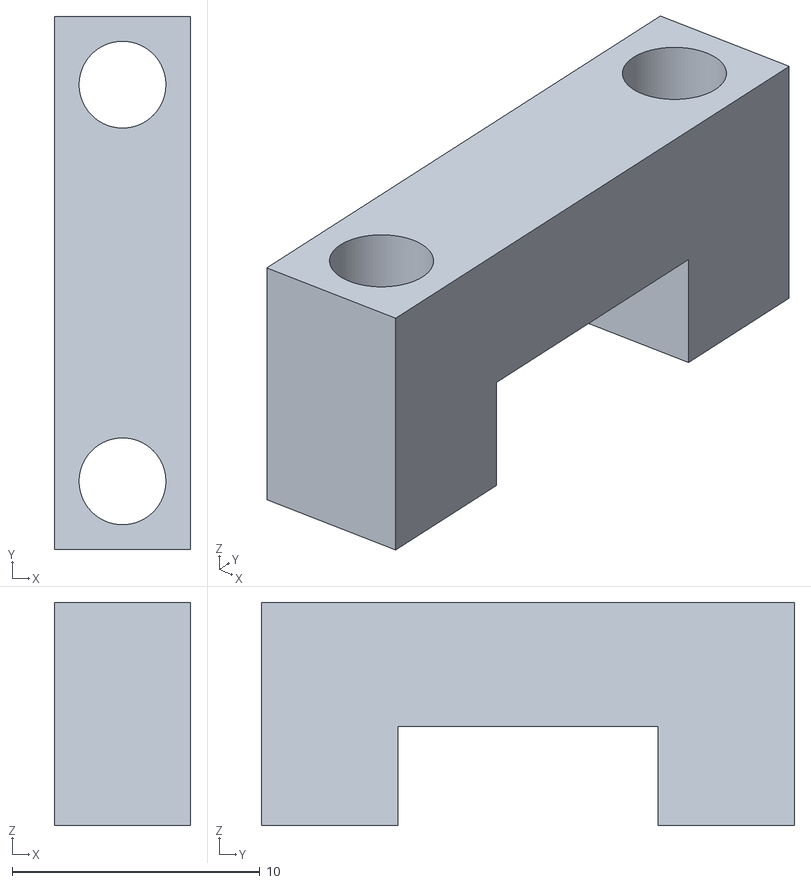
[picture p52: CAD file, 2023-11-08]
CAD/Node_Box/xt60_clampdown.stl
5.50 x 21.5 x 9.00

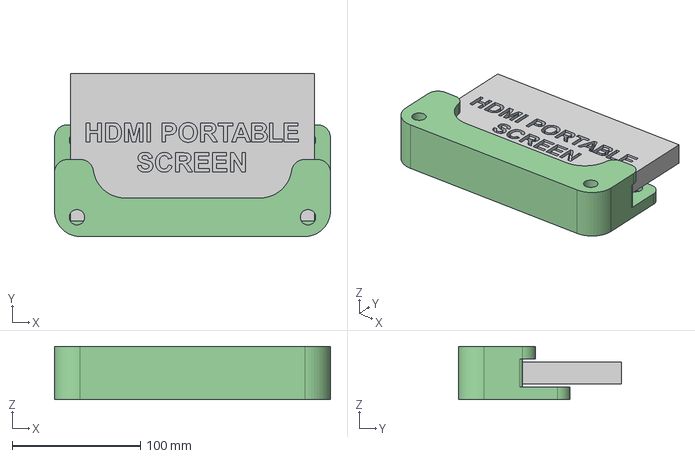
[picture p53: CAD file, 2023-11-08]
CAD/portable_screen_holder/screen_holder.step
215.0 x 127.0 x 41.5 mm
screen
Screem_holder

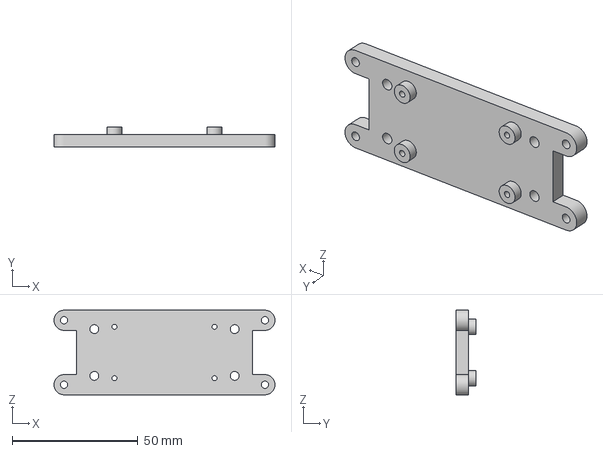
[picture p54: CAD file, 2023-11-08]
CAD/Propulsion_Node_Box/prop_bottom.3mf
87.7 x 8.00 x 33.6 mm

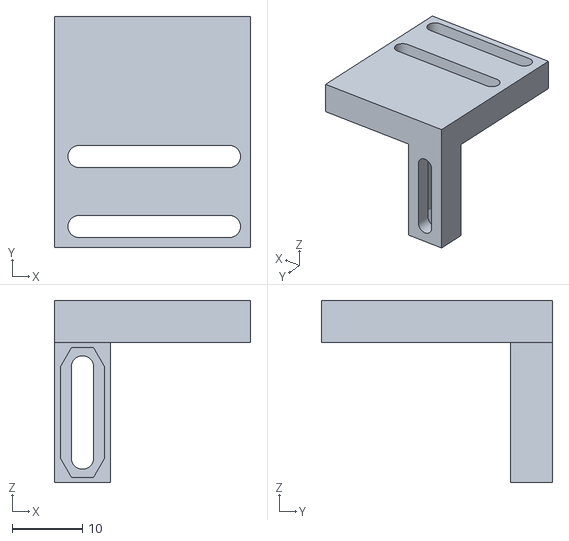
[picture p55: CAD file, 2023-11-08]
CAD/Speed_Sensor_Back/Holder_ajustable.stl
28.0 x 33.0 x 26.0

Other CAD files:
CAD/Speed_sensor_holder/sensor_holder_standing.3mf
CAD/Steering_Node_Box/limitswitch_holder_top.stl
CAD/USB_Hub_clampdown/hub_clampdown_bottom.stl
CAD/wifi_router_holder/xt60_holder.stl
CAD/Arduino_Mega_holder/bottom_nut_holder.stl
CAD/Back_plate_holder/back_holder_thick.f3d
CAD/Back_plate_holder/holder_top.stl
CAD/Battery_BOX/Battery_charger_holder.stl
CAD/Battery_BOX/din_rail_psu_holder.stl
CAD/Battery_BOX/x60_clamp.stl
CAD/Cable_Management/Cable_clip_v1.3mf
CAD/Cable_Management/Cable_management v2.f3d
CAD/Cable_Management/Cable_management_v2.stl
CAD/Cable_Management/big_spiral_holder_1.stl
CAD/Cable_Management/files/Cable_management2.0-3.stl
CAD/Cable_Management/files/Cable_management2.0-4.2.stl
CAD/Cable_Management/files/Cable_management2.0-4.stl
CAD/Cable_Management/files/Cable_management2.0_2.stl
CAD/Cable_Management/spiral_sleve_holders.f3d
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

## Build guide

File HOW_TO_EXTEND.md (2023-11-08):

## Onboarding Procedure
This document is meant to structure the introduction of Autonomous Platform Generation 4 (AP4) to new members. If you feel something was unclear after you read through this, please add to this document to make it easier for future team members!

The goal of this document is for new team members to have a basic understanding of what Autonomous Platform Generation 4 is and how get working within a reasonable amount of time. 

It will describe what prerequisites are required to follow along, how to read through the provided documentation and how to get going continuing the development of the autonomous platform project.

This document does not specify any development tasks - It is up to the supervisor and you to define the goal for the given time period.

### Schedule
Here follows a quick step by step procedure on how to get familiar with the project. You DO NOT need to understand everything, the most important thing is that you get a good overview of the project and get an understanding of where YOU can apply your experience and knowledge to contribute.

Remember, you have a supervisor, be sure to ask for clarifications whenever something is unclear. 

These should be the goals for a new team member. These are simply a guideline and are not set in stone. Talk with your supervisor what parts may be relevant for you or what time plan is suitable. 

#### Week 1

* Understand the purpose of the Autonomous Platform project
* Have a feeling of where certain parts of the project are located at within the repository
* Cloned the repository to your work computer
* Started up the physical AP4 platform by following the startup procedure documentation.
* Read through the major documentation files - Presented in "Where can I find What" Don't expect do understand everything that is mentioned.
* Install needed software (Git, Docker, VSCode, PlatformIO)

#### Week 2

* Start playing around with existing software (preferably on a new git branch to not brake existing functionality). Try to start different components and see if you can get expected output.
* Try and read sensor information from platform and display in terminal. I.e steering angle. Does it change when the wheels are moved?
* Try to control the actuators through command line. Can you set the steering angle?
* Find something that is lacking within the documentation and can be improved upon
* __Decide upon a project which you can perform within a reasonable time frame - Talk with your supervisor what may be suitable for you.__
* Lay out a plan on how to make your project possible. Do you know where in the code to make changes?
* Start internal educations if applicable. (CAN)
* Start external educations if applicable. (Git, Docker, ROS, Linux, etc)

#### Week 3

* Work on your proposed project - Keep your supervisor in the loop
* Continue internal educations if applicable. (CAN, Embedded Development, etc)
* Continue external educations if applicable. (Git, Docker, ROS, Linux, etc)

#### Week 4

* Finished internal educations if applicable. (CAN, Embedded Development, etc)
* Finished external educations if applicable. (Git, Docker, ROS, Linux, etc)
* Work on your proposed project - Keep your supervisor in the loop
* End of week 4: Present the results of your small scale project to some Infotiv members.

## Useful skills/software knowledge

You do not need to be familiar with every software or concept mentioned below.

* Linux Basics and be able to flash OS images to SD cards & USB drives
* Docker containerization basics
* Infotiv AB CAN internal bus education
* Robot Operating System 2 (ROS2) introduction
* Embedded Software Development Introduction

An unpublished copy of the Master's Thesis report is available to read in the repository.

## Extend AP

The process of extending the three specific software components are described in detail in the following documents:

* `CAN_Nodes_Microcontroller_Code/HOW_TO_EXTEND.md`
* `Hardware_Interface_Low_Level_Computer/HOW_TO_EXTEND.md`
* `High_Level_Control_Computer/HOW_TO_EXTEND.md`

### Design Principles

Follow KISS principles:

- "keep it super simple"
- "keep it short and simple"
- "keep it simple and straightforward"
- "keep it small and simple"
- "keep it stupidly simple"

Make subsystems modular, plug-and-play, and independent of each other.
According to Murphy's Law, " Anything That Can Go Wrong, Will Go Wrong", so in other word, things will go wrong in any given situation, if you give them a chance. Make modules that can be replaced and keep each part small and modular. 

### Software

- Emphasize code modularity by utilizing Docker containers.
- Instead of writing installation documents, create a build script (e.g., Makefile) for streamlined setup.
- Include at least one unit test for each module to ensure functionality and reliability.
- Create test scripts to address specific issues and automate the debugging process. For example:
	- For wireless communication issues, implement a bash script that performs ping tests with other nodes.
	- Automate the debugging of CAN communication by utilizing candump in a simple bash script.
- Integrate these tests into your system, running them before executing components for comprehensive validation.
- Ensure well-written and clean code, prioritizing meaningful variable and function names over excessive documentation.
- Be mindful of the side effects of premature optimization and consider them while making performance improvements.

### Hardware

- Utilize standard power sockets and ensure compatibility with standard CAN and power cables/connectors.
- Adhere to standard color coding for wires to ensure consistency and ease of identification.
- Conceal all wires and protect them from accidental disconnection. (assume a kids going to use the gokart)
- Avoid hard wiring between different physical modules/nodes. - Use detachable cables for connections between modules.
- Design all components to be easily opened, inspected, and replaced when necessary.
- Ensure quick and efficient component replacement, similar to the swift tire changes performed during a Formula 1 racing car pit stop. Don't do a Ferrari and make your pit stop more difficult than necessary. 

### Documentation:

- Begin by documenting the "what" and "why" aspects of the project or concept. The focus should be on understanding the purpose and reasoning behind it and "How" is usually not important.
- Begin by documenting the high-level idea or overview before delving into low-level details
- Use markdown format. It is faster, easier and convertible to other more complex format such as LaTeX, HTML and PDF. 

### Prerequisite Software & Skills 
In order to understand the implemented architecture, software and hardware here are some general useful resources:

* Linux Basics and be able to flash OS images to SD cards & USB drives
* Docker containerization basics
* Infotiv AB CAN internal bus education
* Robot Operating System 2 (ROS2) introduction
* Embedded Software Development Introduction

### Adding Wheel Speed Sensor
This is an example procedure on speed sensors should be added onto the platform.

This is an overview of how Fredrik and Erik would have done it but you are free to make your own decision if you follow the principles.

There are supposed to be four wheel speed sensors on the platform. 
The front wheel speed sensors are mounted but not wired.
The back wheel speed sensors need to be 3d printed again.
The wheel speed sensor models can be found in `CAD\Speed_Sensor_Back\`, import stl files into `Ideamaker` 3d printing slicing software, slice model to G-code and print!

The wheel speed sensor hardware, is located in the see-through plastic bin on the platform. 

[link to wheel speed sensor hardware](https://www.conrad.se/p/utbyggnadsmodul-sen-speed-arduino-banana-pi-cubieboard-raspberry-pi-pcduino-1646891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)

The project would be split up in smaller parts (we would start with low level )

0. Set up repository and SW applications
1. Create Embedded-SW close to hardware
	1.1 Create test rig
2. Get hardware sensor working
3. Wire up new ECU base
4. Adjust CAN database & Generate new CAN_DB.c/h files
5. Adjust Low-level Hardware interfacing ROS2 code
	5.1 Adjust can_msgs_to_ros2_topic_pkg package
	5.2 Adjust vehicle controller

So in detail: 

* Install docker
* Clone repository
* Create new personal gitlab branch to work in, Only working code should be added to the main branch. 
* Learning how to use PlatformIO and st-link v2 to flash Bluepill microcontroller in VSCode editor
* (look at Infotiv sharepoint internal educations Edu: Get your first LED blinking on STM32)
* (look in `CAN_Nodes_Microcontroller_Code\HW_NODE_CODE_TEMPLATE\src`)
* Make sure things compile properly and can be uploaded to bluepill microcontroller
* Researching how the speed sensor works
* Create a small local solution test rig, (breadboard and jumper wires, Bluepill and speed sensors)
* Wire Components, Speedsensor
* Some work has been done on this already see the following code (Note:!! not up to date GPIO-pin wise with the standard ECU wiring)
	`CAN_Nodes_Microcontroller_Code\HW_NODE_DEV_Speed_Sensor_Lib\src`
	`CAN_Nodes_Microcontroller_Code\Shared_HW_Node_Libraries\SpeedSensorInterface\src`
* Read the velocity using bluepill board and print result over serial such that one can observe behavior
* Investigate how ECU base is wired (see existing code / documentation)
* CAD files for ECU base are located at `\CAD\Node Box`
* Wire a ECU base, Bluepill, MCP2515, Logic-level-converter, DC-DC converters, ...
* Connect ECU to CAN network, send some dummy data
* understand how to setup linux socket can interface - look into how it is automatically started on raspberry pi
* verify that dummy data shows up on linux cansocket candump
* Adjust CAN database CAN_DB.dbc (dbc file) using kvasar located at `\CAN_Nodes_Microcontroller_Code\CAN_LIBRARY_DATABASE`
* Add new frame(s) for speed measurements
* Generate new C code, CAN_DB.c and CAN_DB.h, see documentation for procedure.
* Compare new vs old CAN_DB.c/.h to see that the changes have been made
* Use the Template code for a ECU and add the speed-sensor-library functionalities
	Make a copy of `\CAN_Nodes_Microcontroller_Code\HW_NODE_CODE_TEMPLATE`
* Create a library in `CAN_Nodes_Microcontroller_Code` for the speed measuring ECU
* Transfer code from test-rig into new created library
* Instead of printing to serial, send velocity over CAN bus
	* See how throttle voltage / steering angle was sent over CAN bus in SPCU library
* Verify that velocity measurements show up on linux socketcan candump
* Append newly created measurement CAN frame (&signals) into the ROS2 can_msgs_to_ros2_topic_pkg source code.
	Located at `Hardware_Interface_Low_Level_Computer\ap4_hwi_code\ap4hwi_ws\src\can_msgs_to_ros2_topic_pkg\src`
	create publishers, subscribers, callback functions, add new switch cases
* rebuild can_msgs_to_ros2_topic_pkg package (colcon build)
* Start the can translator node from can_msgs_to_ros2_topic_pkg
* (It is automatically started if restarting the raspberry pi docker container) or run ROS2 launch file manually
* Use speed measurements for feedback control of velocity in vehicle controller node.
* (Make a copy of `Hardware_Interface_Low_Level_Computer\ap4_hwi_code\ap4hwi_ws\src\xbox_controller_feed_forward_ctrl_pkg`)
* Rename package and add feedback PID/PIDf control theory logic
* Adjust launch file to start the new vehicle controller when docker container is spun up
	See how is currently implemented `Hardware_Interface_Low_Level_Computer\ap4_hwi_code\ap4hwi_ws\src\launch_hwi_software_pkg\launch`

#### Get familiar with the sensor (blink and print)

A good first step is to get familiar with the sensor and understand how to read measurements from it. (Some of these steps could be skipped if experienced working with VScode and programming microcontroller)

1. Clone the AP4 repository and create a new personal gitlab branch to work in. 
  
  NOTE: Do not work in main branch until you know things work.

2. Download VSCode editor, install and learn how to use the Platform IO extension. 
   
3. Make a simple blink script using microcontroller (bluepill, Arduino etc.) connected to a ST-link v2 (used for programming microcontroller). Necessary downloadable software for the ST-link v2 found [here](https://www.st.com/en/development-tools/st-link-server.html). If unsure how to create blink script, refer to the Infotiv sharepoint education: [Get your first LED blinking on STM32](https://infotiv.sharepoint.com/sites/Educations/Delade%20dokument/Forms/AllItems.aspx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). Make sure things compile properly and can be uploaded to the microcontroller.
   
4. Research how the sensor works (pin ports, operating voltage etc.).
   
5. Create a small local solution test rig and wire components (breadboard, jumper wires, microcontroller, ST-Link v2, USB-mini and sensor).
   
6. Read the sensor measurement using the test-rig board and print the result over the serial monitor in VSCode. 

#### Adding a new CAN frame

It is recommended to have completed the [internal Infotiv CAN education course](https://infotiv.sharepoint.com/sites/Educations/Delade%20dokument/Forms/AllItems.aspx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) beforehand.

1. Adjust the existing CAN_DB.dbc (dbc file) located under `/CAN_Nodes_Microcontroller_Code/CAN_LIBRARY_DATABASE`. It is recommended to use KVASER database editor for this, as it provides a simple interface for adding frames and signals. Download link to Kvaser database editor found [here](https://kvaser-database-editor.software.informer.com/2.4/). A video explaining how to use it found [here](https://www.youtube.com/watch?v=mAL1Xo2G9-4). More specific information related to AP4 found in README.md under [`CAN_Nodes_Microcontroller_Code`](CAN_Nodes_Microcontroller_Code).
   
2. Add new frame(s) and signal(s) for sensor measurements similar to figure below.  

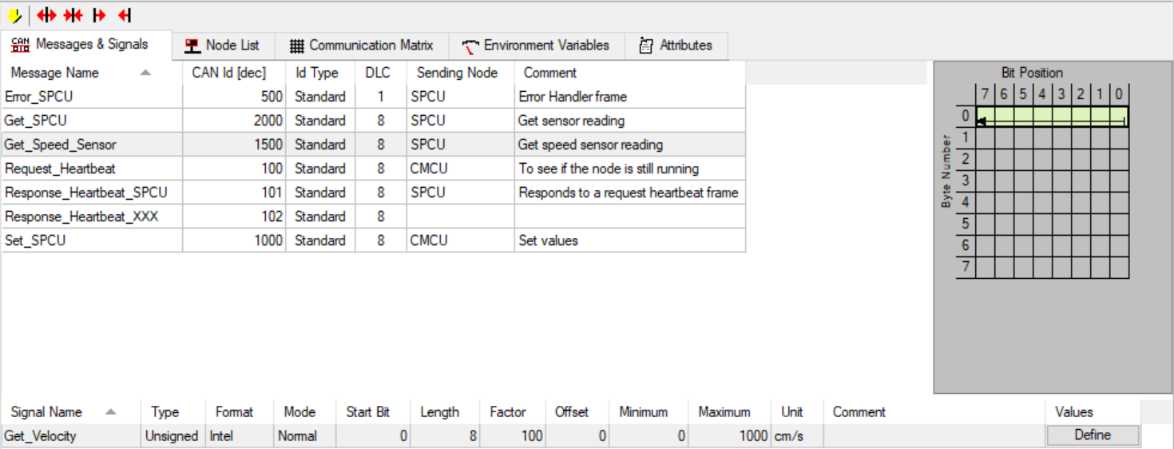
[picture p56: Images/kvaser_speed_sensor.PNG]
Kvaser speed sensor


NOTE: Use Linux PC for next step (step 3). Push updated CAN_DB.dbc file to git repo. and git pull main branch on Linux PC.

1. Generate new C code: CAN_DB.c and CAN_DB.h, documentation how this is done found under [CAN_LIBRARY_DATABASE](CAN_Nodes_Microcontroller_Code/CAN_LIBRARY_DATABASE).
   
2. Compare new vs old CAN_DB.c/.h to see that the changes have been made.

NOTE: Push changes to git repo and git pull main branch on a Windows PC.

#### Code Sensor to CAN message

1. Use the ECU template code found under [`CAN_Nodes_Microcontroller_Code/HW_NODE_CODE_TEMPLATE`](CAN_Nodes_Microcontroller_Code/HW_NODE_CODE_TEMPLATE). Check the comments inside the source code and get an overall understanding of the different steps.

2. Extend the code with CAN message decode/encode and sensor functionality.

TIP: Check previous ECU codes (SPCU and Speed_sensor ECU) located under [`CAN_Nodes_Microcontroller_Code`](CAN_Nodes_Microcontroller_Code) to see which additions need to be made.

In short, what needs to be added to the ECU template are:
- Inclusion of any additional library.
- Specify global variables.
- Specify configurations such as input/output pin ports and baud rate.
- can_interface.AddPeriodicCanSend(CAN_ID,time) inside setup() function.
- Sensor algorithm, decode and encode CAN frame inside loop() function.
  The format of the decode and encode messages can be found inside the generated CAN_DB.h file, example from another sensor can be seen below.

Velocity encode decode

1. Make sure the code is buildable and upload the code to the microcontroller.
   
#### Build an ECU

1. Extended the test-rig built in *Get familiar with your sensor* and add a CAN module.

NOTE: Look through the specifications of the components to understand each pin port, operating voltage and how to connect everything.

2. Connect a DB9 connector between the CAN module test-rig and the Raspberry Pi mounted on AP4. Update the files on the Raspberry Pi by powering on AP4 using the flip switch, navigate on the display using the wireless mouse and keyboard (labeled Infotiv 3) and git pull the repo.
   
#### Raspberry Pi 4b 4gb

3. Verify that sent CAN messages from the microcontroller show up on the Linux cansocket candump. On the Raspberry Pi this is done by opening a new terminal and running the command:
```bash
candump can0
```

Below you can see an output example from candump. It shows which channel the message is being transmitted on (can0), the ID (5DC), the frame size [8 bits] and the data bits (00 00 ...).

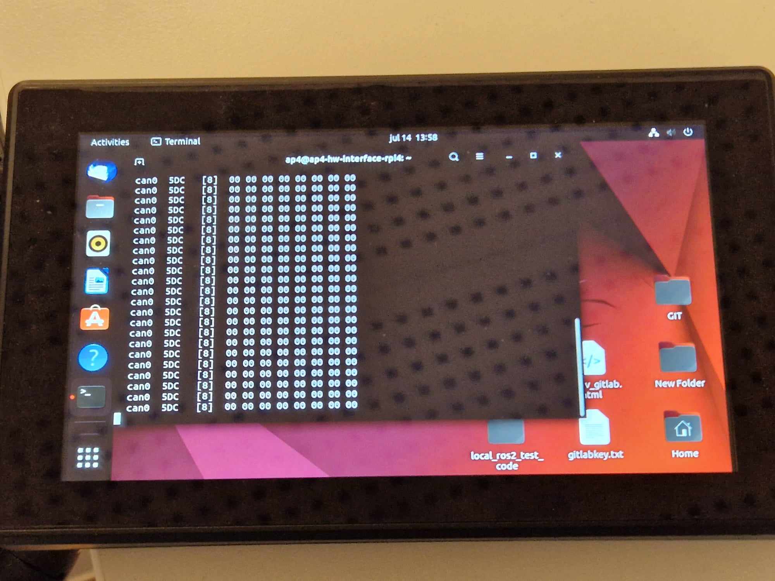
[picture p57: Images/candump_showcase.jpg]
candump


#### CAN to ROS communication

1. Append newly created measurement CAN frame (&signals) into the ROS2 [can_msgs_to_ros_2_topic_pkg source code](Hardware_Interface_Low_Level_Computer/ap4_hwi_code/ap4hwi_ws/src/can_msgs_to_ros2_topic_pkg/src/can_msgs_translator_interface.cpp). This procedure is pretty straight forward and a detailed description can be found under [Hardware_Interface_Low_Level_Computer](Hardware_Interface_Low_Level_Computer).
   
2. Git push the changes and git pull repo on the development laptop (Linux).

#### Development laptop

1. Rebuild can_msgs_to_ros2_topic_pkg package (colcon build). The procedure is described under [Hardware_Interface_Low_Level_Computer](Hardware_Interface_Low_Level_Computer).

NOTE: For the next step it is important that both the Raspberry Pi and the Development laptop are connected to the same wifi/ethernet. This can be double checked using a simple "Ping test", which tests their communication.

Restart the Raspberry Pi and Development laptop and use the following commands in a new terminal on respective device:

#### On the Raspberry Pi
- Enter the existing docker container 
```bash
docker exec -it ap4hwi bash
```

- Source variables
```bash
source /opt/ros/humble/setup.bash
``` 
- Start the CAN translator node
```bash
ros2 launch ros2_socketcan socket_can_bridge.launch.xml
``` 

#### On the Development laptop

- In the terminal, navigate to `/High_level_Control_Computer`
- Build the docker container
```bash
docker-compose build
``` 
- Disable the access control (necessary in order to start the container)
```bash
xhost +
``` 
- Start the docker container
```bash
docker-compose up
``` 
The Gazebo environment should start up, ignore this for now.

- Double check that the docker container is up and running 
```bash
docker ps
``` 
- Open a new terminal window and enter the docker container
```bash
docker exec -it ap4hlc bash
``` 
- Source variables
```bash
source /opt/ros/humble/setup.bash
``` 
- View topics on the ROS network
```bash
ros2 topic list
``` 
- If everything works, the sensor message should appear under the topic named /from_can_bus. This can be viewed by running the following command:
```bash
ros2 topic echo /from_can_bus
```

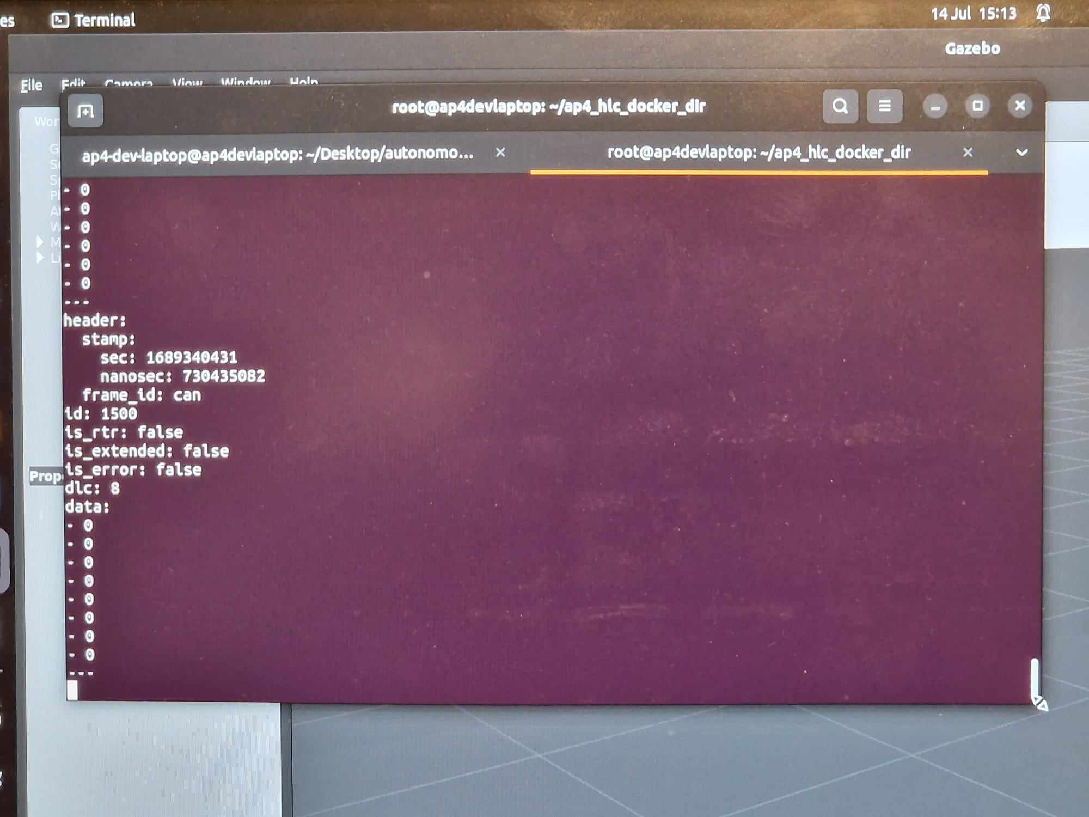
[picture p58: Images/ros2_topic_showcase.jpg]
ROS2 topic showcase


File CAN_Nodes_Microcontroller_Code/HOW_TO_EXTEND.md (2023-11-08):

## How to extend Embedded Software
This document aims to describe to process of how to extend the hardware interface and low level software.

Before starting to develop and adding code to the embedded software you need to first make sure you need to add something here. 

If you;

* Want to add an embedded sensor / actuator
* Need to add a new CAN signal or frame to existing sensor / actuator

Then you are in the right spot!!  If not, take a look at `Hardware_Interface_Low_Level_Computer` or `High_Level_Control_Computer`, maybe you intended to add functionality there!

### Prerequisites

In order to start adding functionality it is recommended to have a basic understanding of:

* C++ OR Python development
* Embedded Development
* CAN bus
* docker containers (How to start, stop, restart and configure)
* Basic Linux - The container software environment is mainly navigated in through a terminal

Software wise, you need to have the following installed:

* docker
* git
* VSCode (recommended but any IDE may be suitable)
* PlatformIO extension

Hardware wise, it is recommended you have:

* Linux based x86 host computer 

### Add New Functionalities

First of all make sure you have read the general design principles document for autonomous platform generation 4 located at `autonomous_platform/HOW_TO_EXTEND.md`. This document takes precedence over anything written in this document in order to unify the development process across all software layers.

### Standard base ECU
Autonomous platform generation 4 uses a standard base ECU (Electronic Control Unit) meaning every embedded software should use the same hardware. The ECU or node box has a standardized Input and Output. ECUs are connected together in a CAN bus network, this network contains the Hardware Interface hardware, the Raspberry Pi 4b, which links the network with higher level software. Onto the base ECU specific hardware for a specific function can be added. For example, for the SPCU (Steering Propulsion Control Unit) there are DACs and Motor Controller hardware connected to the ECU.

Inputs:

* CAN bus passthrough (Through DB 9 connector)
* 12v Power (Through XT60 connector)

Outputs:

* CAN bus passthrough (Through DB 9 connector)
* 5v Power
* 3.3v Power
* GPIO pins

It is preferred to build a new ECU node when adding functionality to autonomous platform to prevent breaking existing functionality. ECUs should preferably

If new functionality cannot be implemented on an existing ECU node, a new hardware node must be built. See [How to Build new ECU](#how-to-build-a-new-ecu).

### build a new ECU
1. Start 3D printing generic ECU components (top, bottom, internal component holders)
Please check `CAD` folder for the list of components that need to be printed. 

The estimated material consumption (with reasonable slicer settings) is around 200 grams. And total print time is around 16-18 hours. Grab some coffee and leave it printing overnight! Make sure the first layers stick properly to the printing bed before leaving.

Note: Make sure you add supports manually for the print-in-place XT60 connector clampdowns. Any other support is not strictly necessary. These are circled in red below.

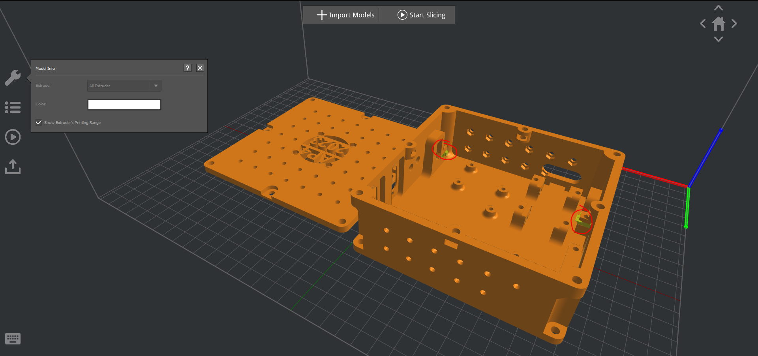
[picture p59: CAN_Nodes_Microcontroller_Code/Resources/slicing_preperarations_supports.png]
Slicer supports


2. Make sure all components are working individually before mounting them inside the node.
    I.e flashing the bluepill, measuring output from dc-dc converters, making sure the MCP2515 can bus board is working

A schematic illustration of the components inside the generic ECU can be seen below.

ECU - speed sensor block diagram

3. Once 3D print is complete, remove added support material for the XT60 clampdowns

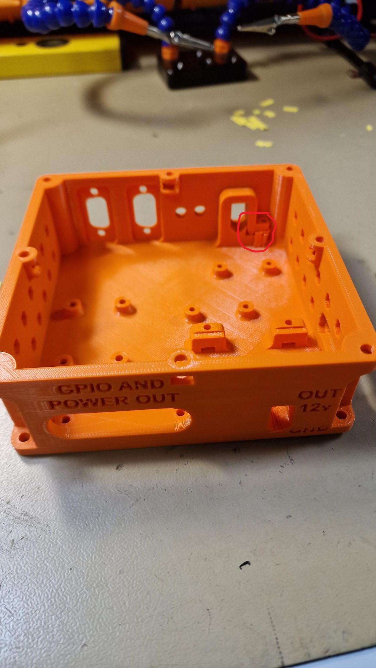
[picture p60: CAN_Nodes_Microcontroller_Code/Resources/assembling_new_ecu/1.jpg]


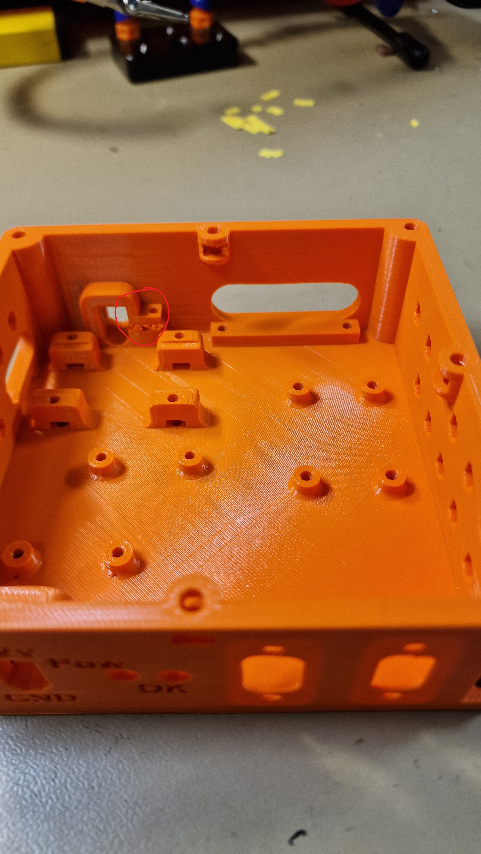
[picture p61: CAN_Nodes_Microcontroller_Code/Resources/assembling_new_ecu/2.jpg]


4. Insert 12 M3 nuts in the hex shaped holes on the underside

Note: The hole circled in blue shall also have a m3 nut.

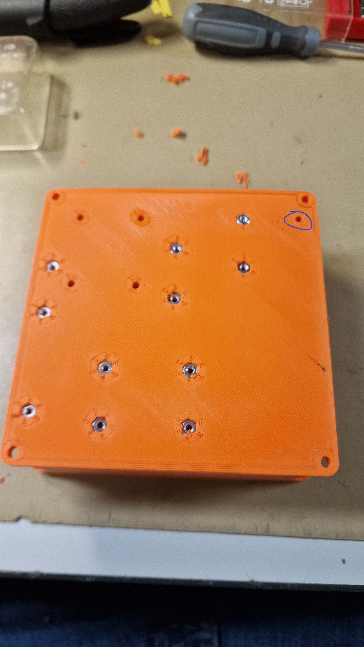
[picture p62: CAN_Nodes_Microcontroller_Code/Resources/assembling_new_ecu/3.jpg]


5. Assemble power distribution and mount inside HW node.

A schematic for the power distribution inside the HW node can be found below.

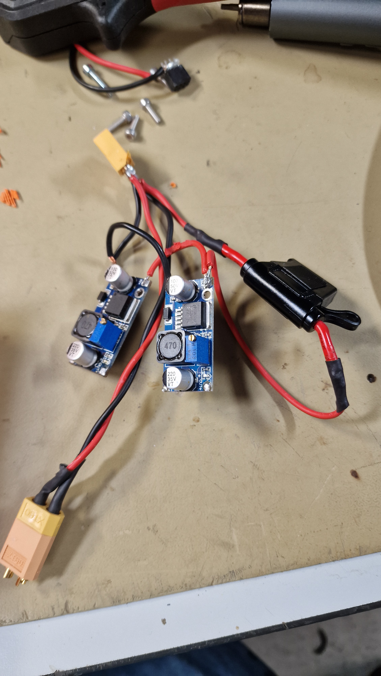
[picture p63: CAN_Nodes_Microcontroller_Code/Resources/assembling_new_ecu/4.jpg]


6. Mount power distribution inside node.

The XT60 contacts are inserted into the 3D printed clamp. The DC-DC converters are screwed in with 2 M3x10mm screws respectively.

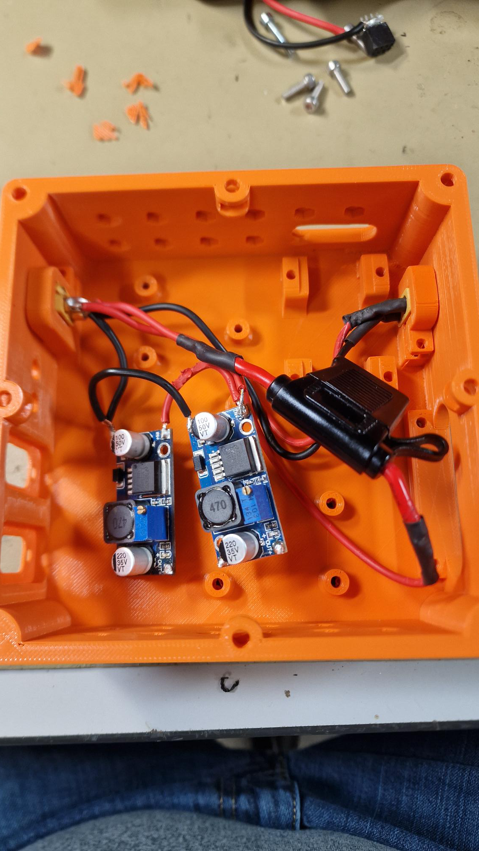
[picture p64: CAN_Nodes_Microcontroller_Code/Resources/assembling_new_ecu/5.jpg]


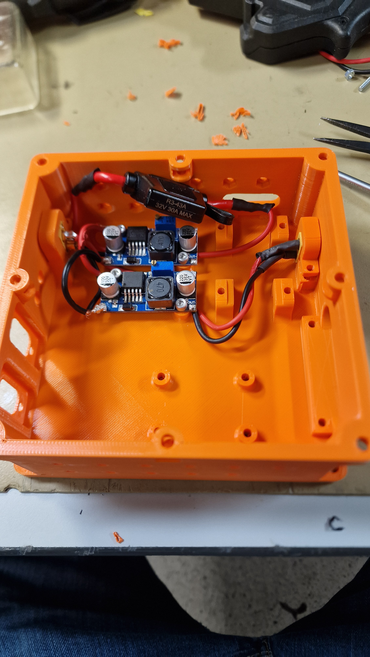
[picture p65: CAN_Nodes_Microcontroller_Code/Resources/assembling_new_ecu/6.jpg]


7. Assemble CAN module and D-Sub 9 connectors.
A wiring diagram can be found below.

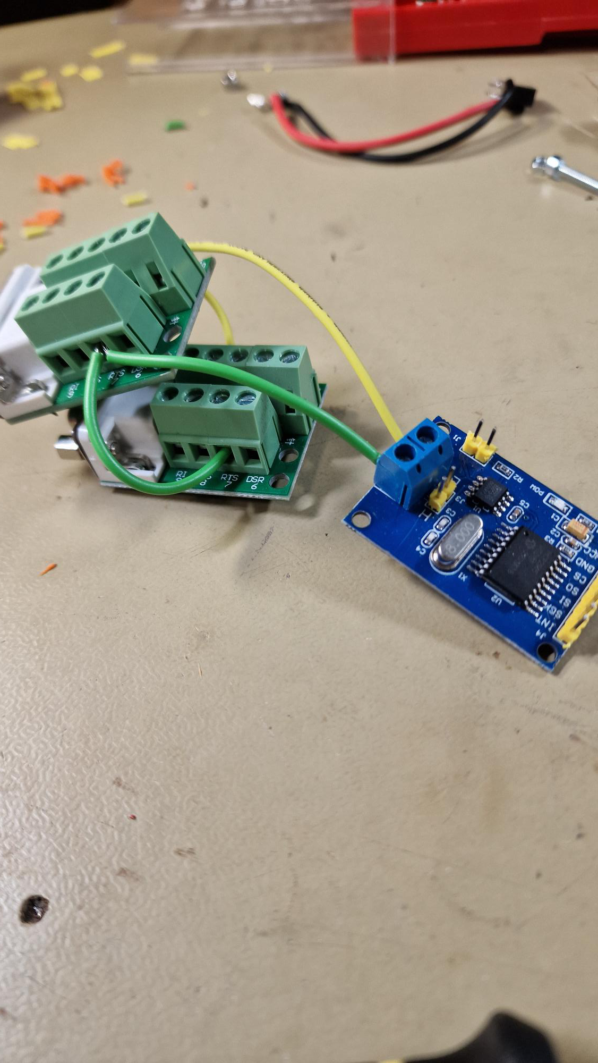
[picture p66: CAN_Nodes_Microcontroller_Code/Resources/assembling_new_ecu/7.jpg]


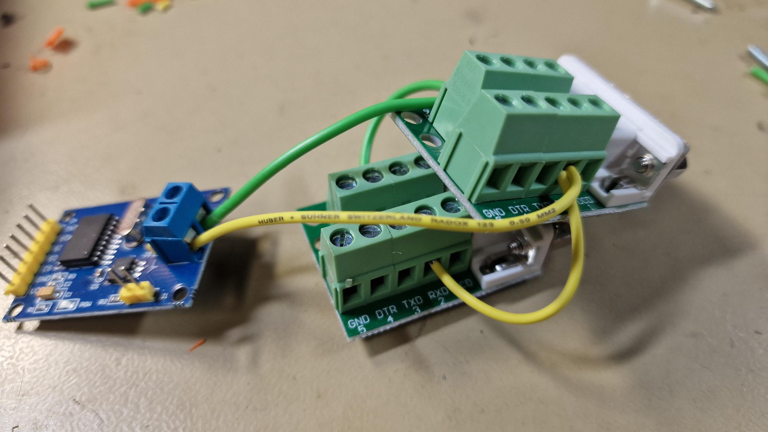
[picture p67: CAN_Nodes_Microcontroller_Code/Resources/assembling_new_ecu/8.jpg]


8. Mount CAN module and D-Sub 9 connectors inside HW node.

D-Sub 9 connectors are screwed in from outside. The MCP2515 card is screwed in with two M3x10mm screws.

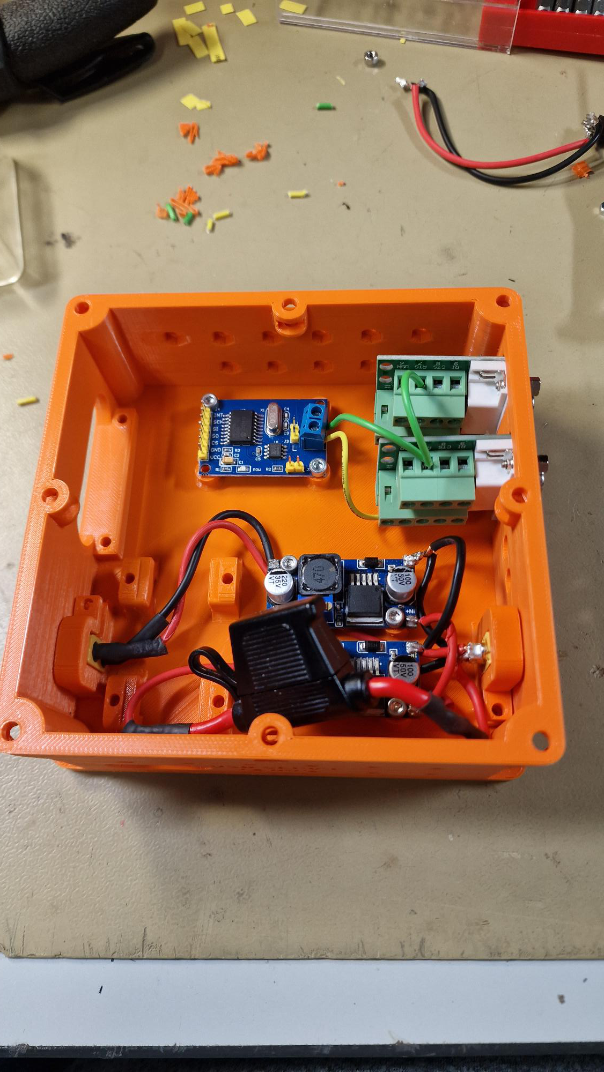
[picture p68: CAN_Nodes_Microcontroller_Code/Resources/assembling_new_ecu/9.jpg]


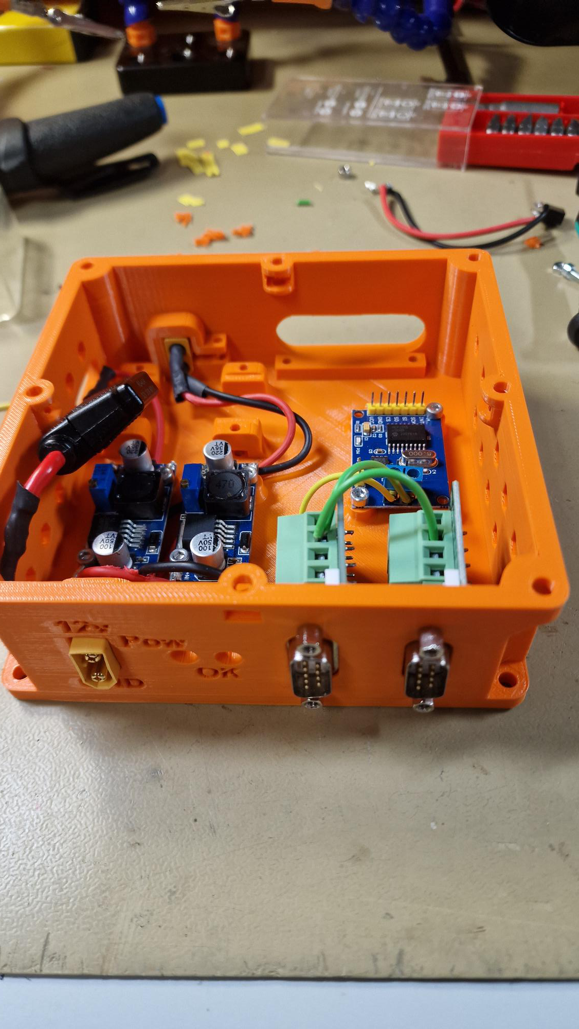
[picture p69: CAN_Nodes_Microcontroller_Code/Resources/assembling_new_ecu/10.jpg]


9. Insert 4 M3 nuts inside  STM32 hold down pillars. Make sure the hole in the pillars align with the inserted nuts.

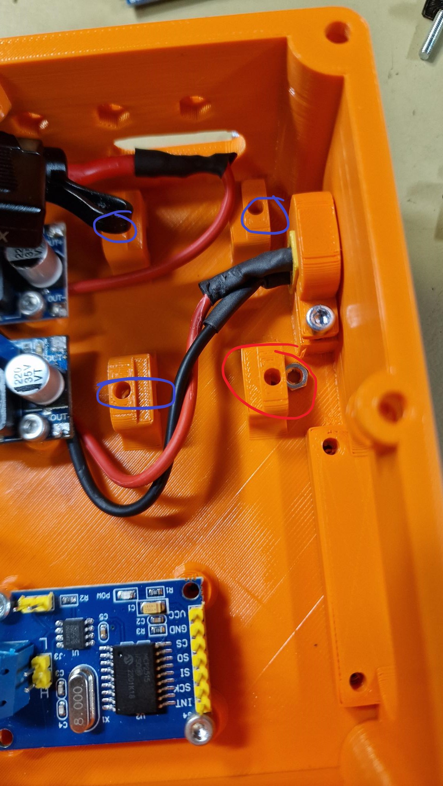
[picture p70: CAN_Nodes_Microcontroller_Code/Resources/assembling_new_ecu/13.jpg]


10. Wire programming pins for STM32 Bluepill

The programming wires shall have the following colours:

| **STM32F103C8T6 Bluepill Pin** | **Wire  Colour** |
|:---:|:---:|
| 3.3v | Red |
| IO | Brown |
| SCLK | White |
| GND | Black |

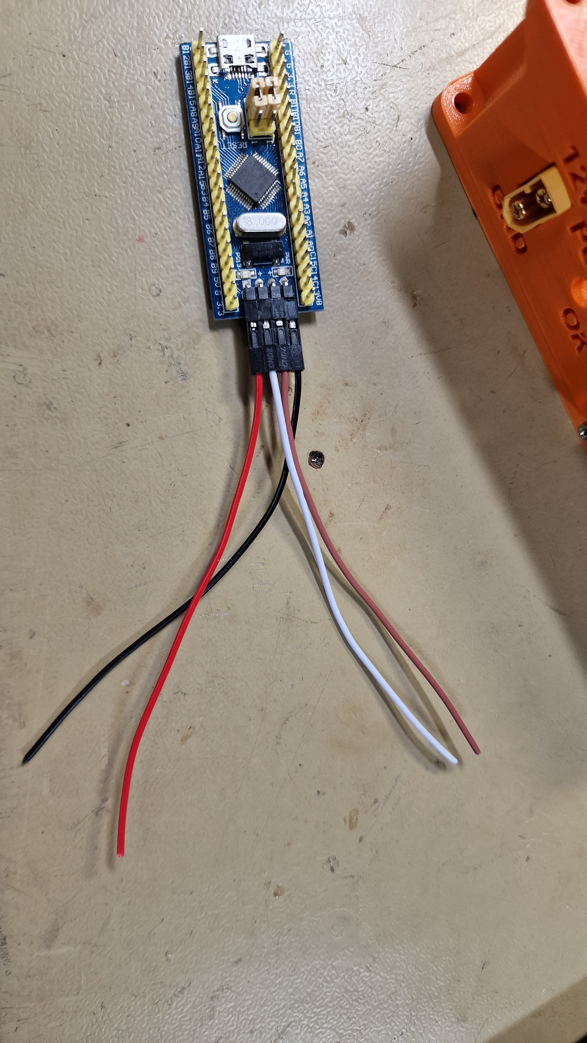
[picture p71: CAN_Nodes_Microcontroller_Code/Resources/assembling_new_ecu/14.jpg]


11. Using 4 STM32 bluepill clampdown (3D printed) tabs, clamp down the STM32 bluepill microcontroller.

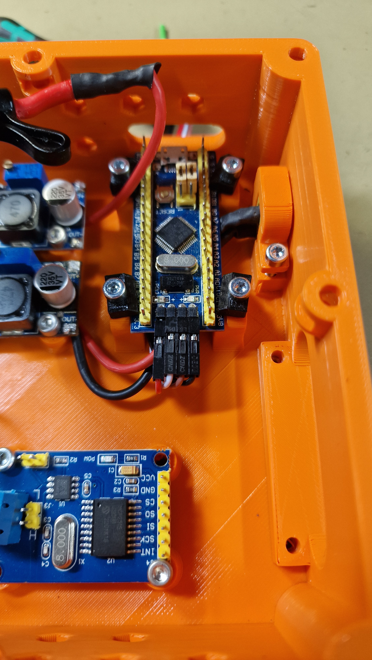
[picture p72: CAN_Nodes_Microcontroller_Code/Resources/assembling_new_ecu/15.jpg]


The four wiring cables shall be passed through to the side of the HW node.

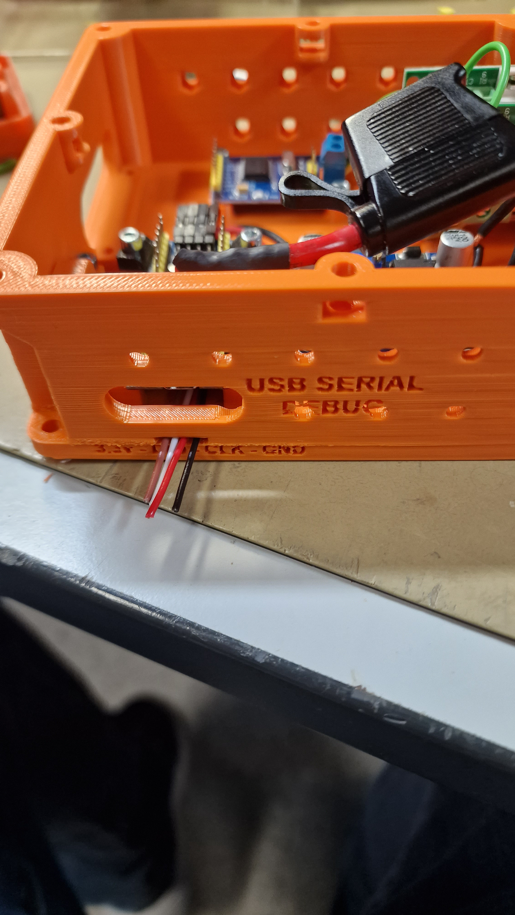
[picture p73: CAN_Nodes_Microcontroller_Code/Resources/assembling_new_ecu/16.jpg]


Cramp JST SM 2.54 female connectors on the outgoing programming wires. Insert a heat shrink cable over the cables.

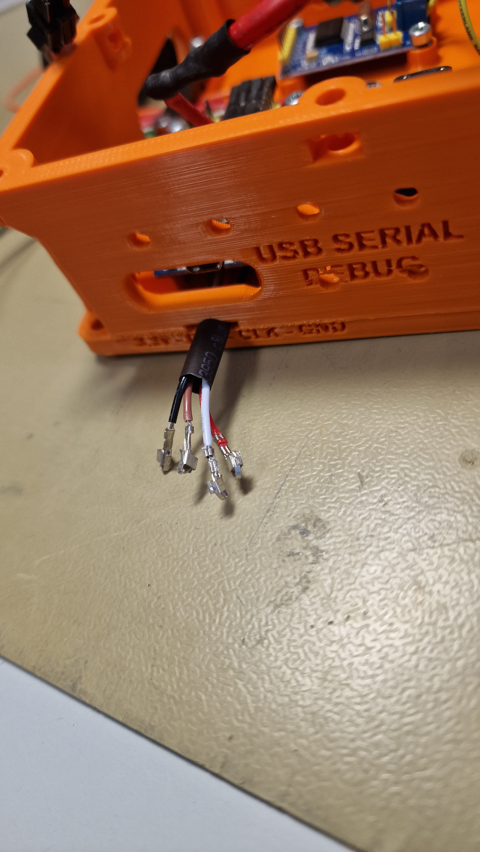
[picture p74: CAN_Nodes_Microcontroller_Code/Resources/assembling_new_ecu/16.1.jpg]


Insert the female JST SM 2.54 crimped connectors into a male JS connector as seen below, it is important that the colour and placement are the same between ECU nodes.

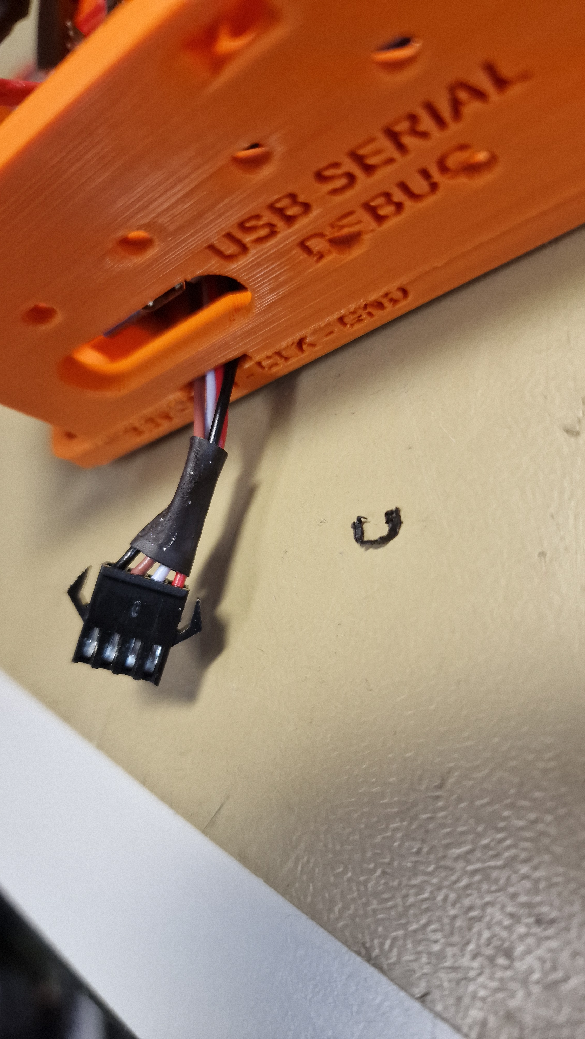
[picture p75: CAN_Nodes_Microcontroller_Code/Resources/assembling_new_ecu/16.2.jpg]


12. Screw down the outgoing cable hold-down (3D printed component). Use two M3x16mm screws.

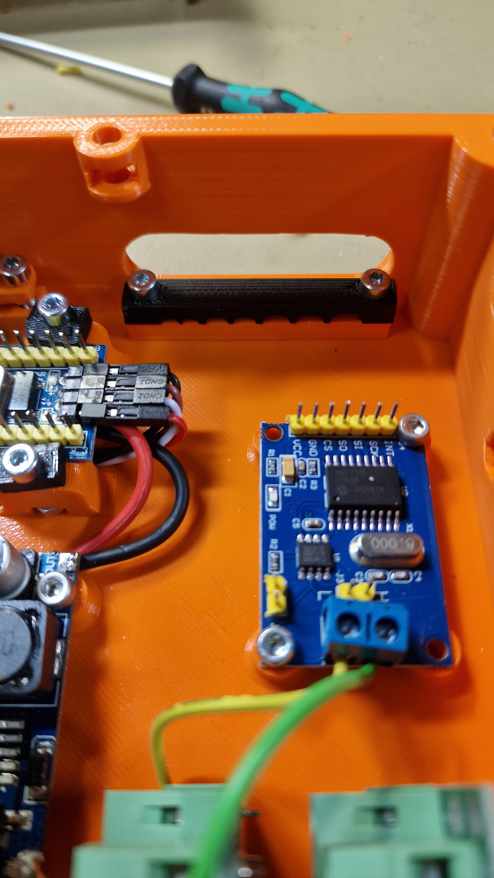
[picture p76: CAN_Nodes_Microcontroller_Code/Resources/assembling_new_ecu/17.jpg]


13. Installing 12v dc fan for cooling. A cooling fan should be screwed into the top cover of the ECU using 4 M3 screws and nuts.

First, cut the fan cable in two pieces.

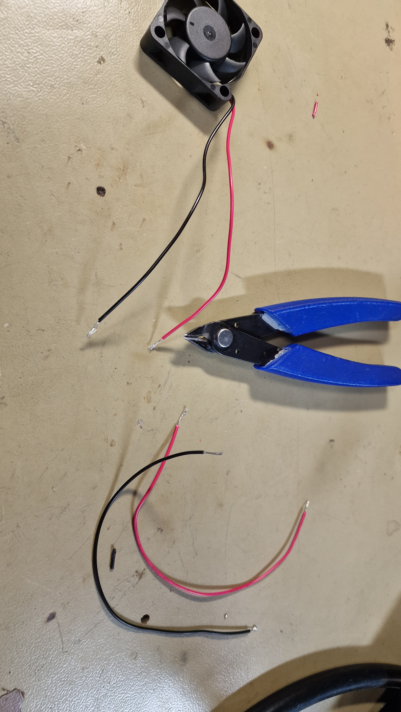
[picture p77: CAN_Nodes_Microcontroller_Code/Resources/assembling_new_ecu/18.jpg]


Connect the two cables together using JST SM 2.54 2 pin connector. This is to make the top cover completely removable if desired.

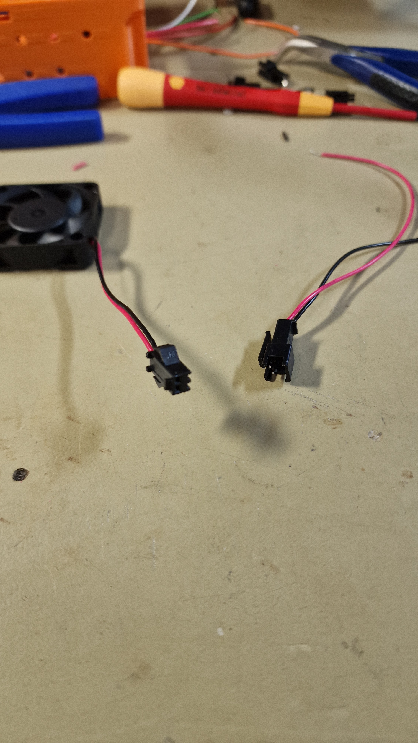
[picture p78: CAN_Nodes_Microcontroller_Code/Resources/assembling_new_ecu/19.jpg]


Solder the fan +12v and GND to the power in. (After the fuse). This can be done by connecting the wires to the dc-dc converters in terminals.

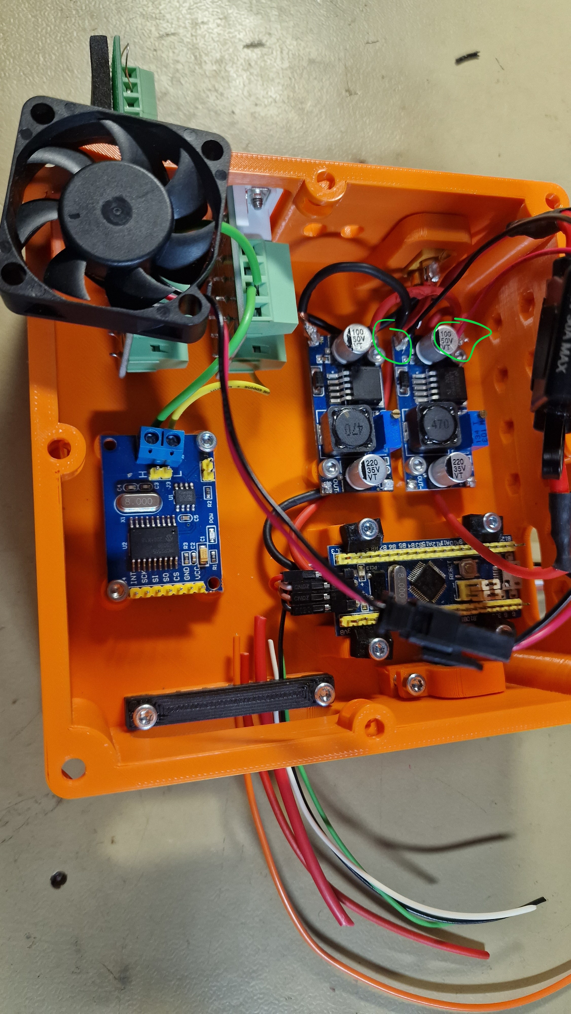
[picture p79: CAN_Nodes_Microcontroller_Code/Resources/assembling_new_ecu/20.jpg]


The fan shall then be mounted to the top cover as illustrated below. Using 4 M3x16mm screws and 4 M3 nuts.

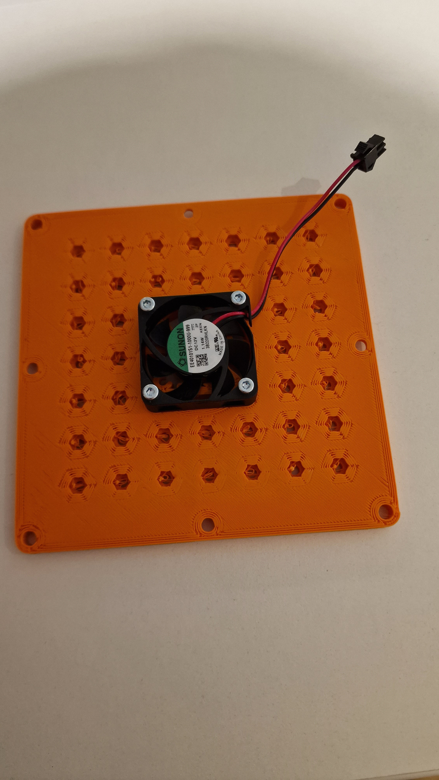
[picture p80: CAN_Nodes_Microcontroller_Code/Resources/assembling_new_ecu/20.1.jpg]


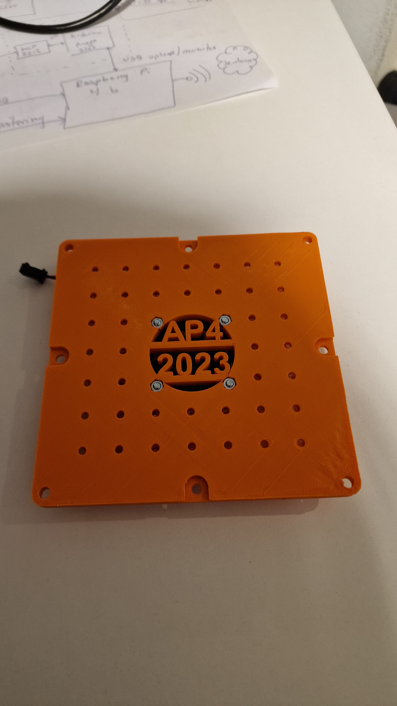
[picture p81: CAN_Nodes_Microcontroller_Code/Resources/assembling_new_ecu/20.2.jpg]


14. Power up module

To verify that the previous steps have been done correctly, connect 12v to the XT60 12v in plug on the front.

The expected result would be that the fan turns on and the dc-dc converters light up with a led shining. 

The center dc-dc converter should output 3.3v and the dc-dc converter closest to the wall should output 5v.

If it does not power up correctly;

* Make sure you have inserted a 2A, 3A or 5A fuse into the fuse holder
* Check soldering connections using a multimeter

If dc-dc converter out voltage is not correct, adjust the blue potentiometers with a screwdriver until desired voltage is reached.g 

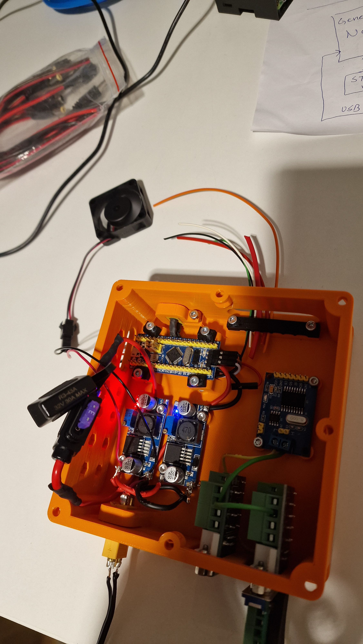
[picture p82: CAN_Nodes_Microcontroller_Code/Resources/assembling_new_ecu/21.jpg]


15. Internal wiring of standard components. This can be done with either jumper wires or soldering new wires between internal components.

Here is the wiring diagram for a generic ECU HW node.

The internal wiring of a ECU can be seen bellow. This has to be setup in order to run software on the bluepill microcontroller and communicate over CAN bus.

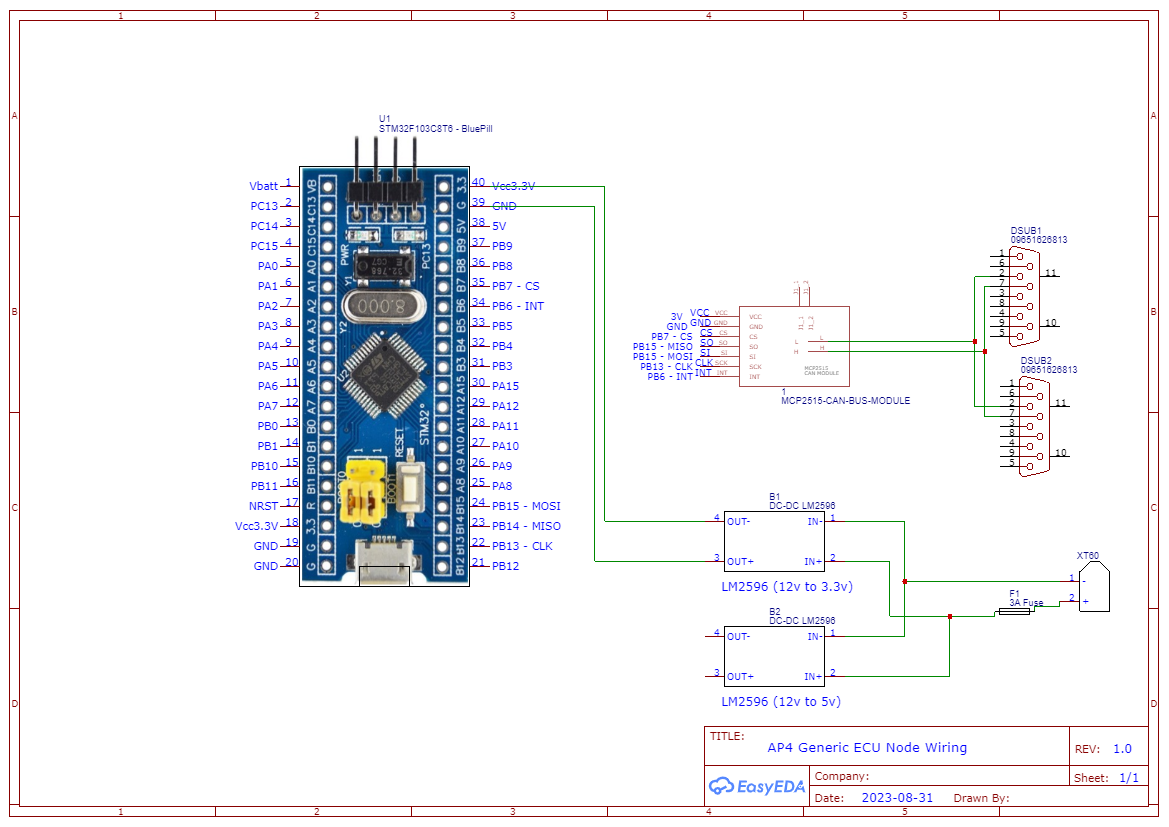
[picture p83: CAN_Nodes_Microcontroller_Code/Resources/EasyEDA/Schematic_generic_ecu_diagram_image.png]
Internal wiring schematic of generic ECU


16. Mount top cover onto ECU node.

The top cover can be mounted as pictured below using 4 M4x10mm screws and 4 M4 nuts.

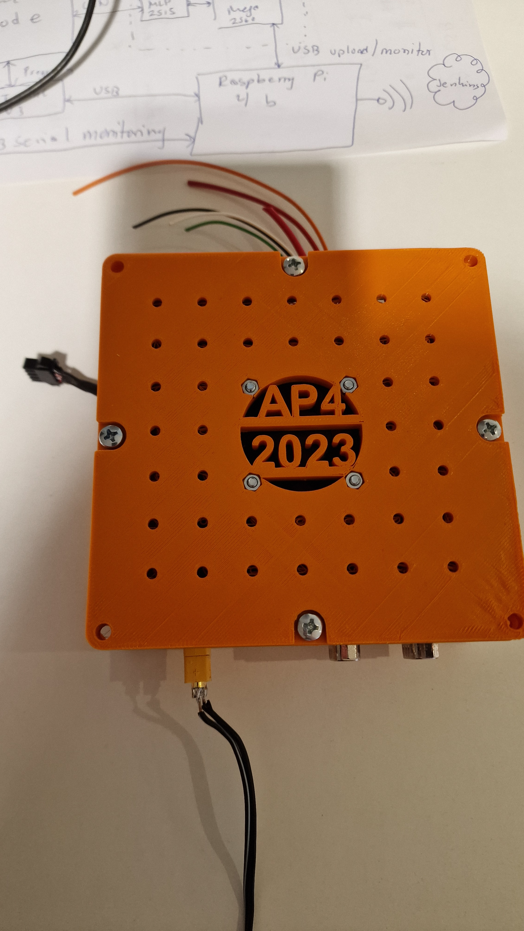
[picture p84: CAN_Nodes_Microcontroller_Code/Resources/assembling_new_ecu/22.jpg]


17. Connect any needed embedded sensor(s)

Note done the extra wiring required and how you connected it and add to the node specific documentation.

18. Flash new software

How to flash new software to the STM32 bluepill can be found in the `HOW_TO_PROGRAM_A_BLUEPILL.md` document.

### Extend with new function specific ECUs

These are the general guidelines and tips when adding a new function (or sensor) to a generic ECU base.

Questions to ask yourself;

* How can the sensor be connected to a microcontroller? Does it require any communication protocol or can you use a digital or analog pin?
* What power requirements does it have? High power or low power? If the sensor/actuator requires more power (and or different voltage) from what the generic ECU can supply you need to take this into consideration
* Am I adding new functionality to an existing ECU or am I adding completely new functionality? Maybe it is not necessary to build a new ECU node from scratch
* What parts do I have in inventory?
* What parts do I have to buy?

Very briefly explained, here are the steps you should take to implement new functionality with embedded sensors or actuators.

- Add specific hardware modules
- Built a small test-rig with a microcontroller & breadboard to verify functionalities and software libraries needed.
- Build, solder and connect a generic ECU base (see SPCU). Interface the specific hardware module.
- Create a CAD model of the new sensor and how it should be mounted to the platform. (Make sure it fits the standardized hole pattern if it should be mounted to an ECU or aluminum sheet)

- If needed, update the CAN protocol by editing the dbc file and autogenerate new database in c-format.

- Copy the Template code for ECUs.
- Flash both the ECU and central master computer (update the CAN to ROS2 topic converter) with the latest CAN protocol. See `HOW_TO_EXTEND.md` in `Hardware_Interface_Low_Level_Computer` directory
- Add generic ECU code in the embedded software, follow the structure of the SPCU.
- When the embedded software of the ECU is verified, connect the to the rest of AP4 using a db9 Female-Female cable and a xt60 outlet to supply.

### Unified CAN database and how to modify 

The CAN database follows dbc format, [CAN and dbc guide](https://www.csselectronics.com/pages/can-dbc-file-database-intro). The dbc file can be edited using a dbc-editor an example of this is the [KVASER-DATABASE-EDITOR](https://kvaser-database-editor.software.informer.com/2.4/). When opening the dbc file for AP4 in kvaser, it will look like the figure below:

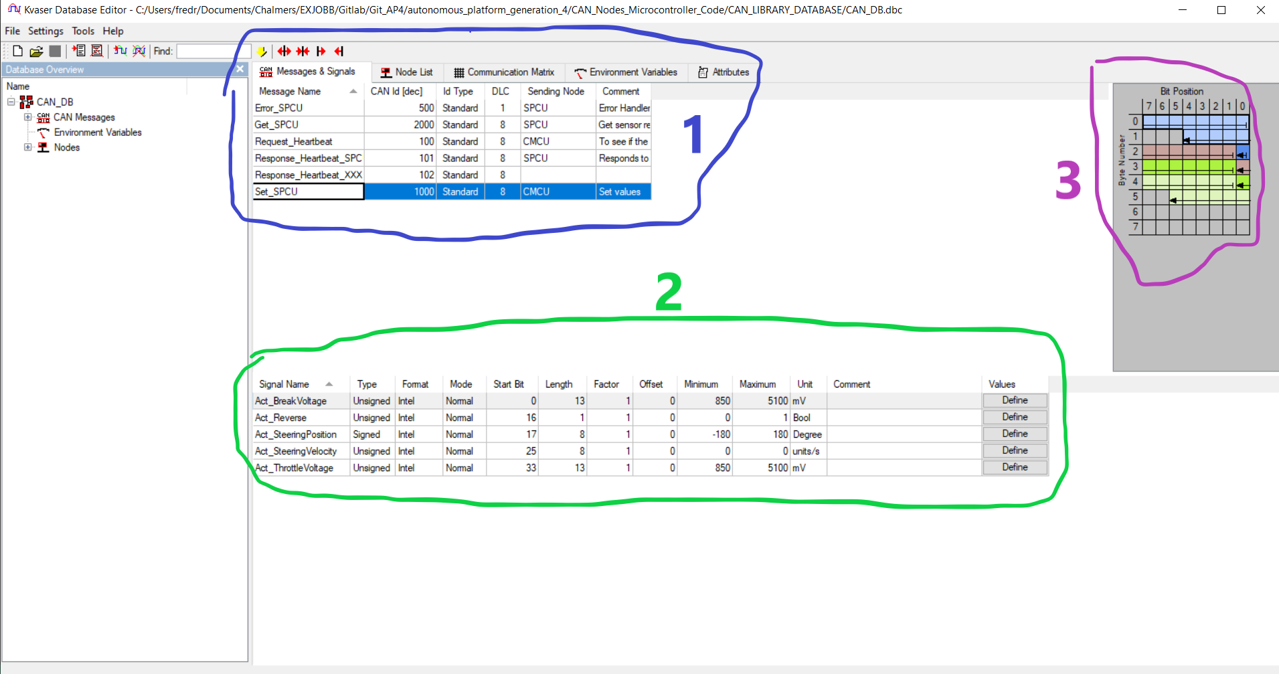
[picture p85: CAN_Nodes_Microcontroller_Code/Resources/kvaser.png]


1. **Message Name** in the database. This is the frames defined for a CAN message. What id, Data length (bytes) etc.
2. **Signals** in each message. User defined regarding name, placement in the data-field, offsets, factor and so on.
3. **Graphical Illustration of datafield** for the selected message/frame in the database.

In order to make sense of the dbc files, the embedded software needs the information of the dbc file in a c format. Thus AP4 converts dbc file into c-functions and data types, in order to simply encode and decode. Using [howerj dbcc repo](https://github.com/howerj/dbcc) to convert.



When the dbc is edited and saved, run the following command in a **Linux Machine** whilst located in path: `CAN_Nodes_Microcontroller_Code\CAN_LIBRARY_DATABASE`

```bash
. create_database_from_dbc_script.sh
```
Down below is a simple flowchart of the way of working with the CAN protocols auto generation and dbc editing.

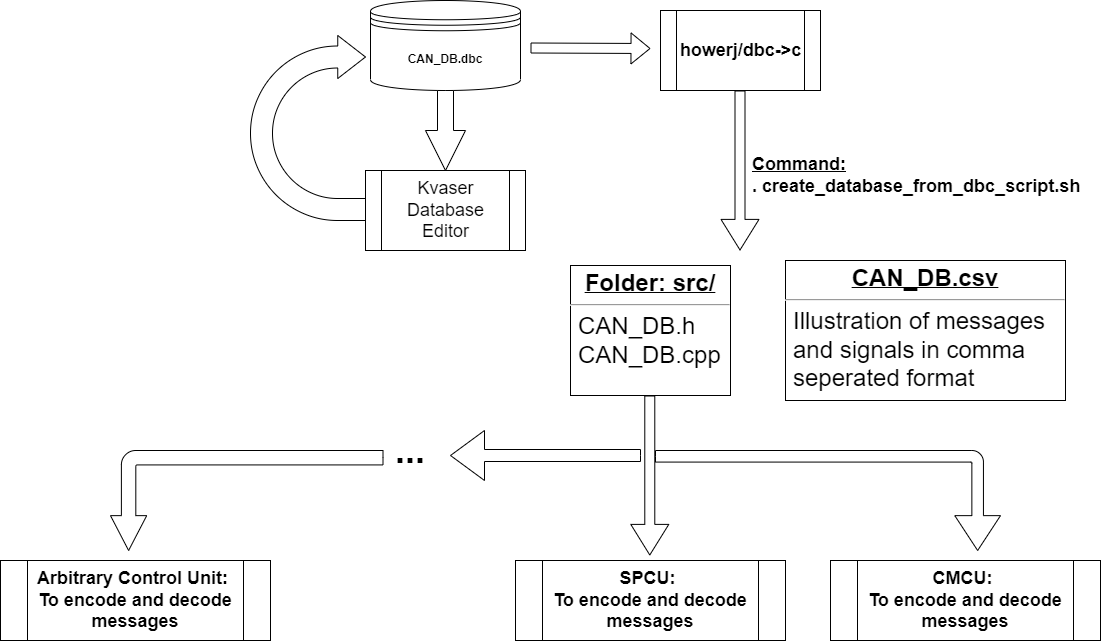
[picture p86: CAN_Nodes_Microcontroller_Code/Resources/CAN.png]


Down below can be seen how all the Software components refers to the same database meaning that a change in the CAN protocol at a single place will affect the whole system.



Also can be seen above how the central master computer, converts CAN messages to ROS2 topics to be later used in higher level algorithms. The *CAN signals To ROS2 Topic Converter* is illustrated in the figure below, implemented on the Raspberry Pi4b that acts as an interface in the central unit. The converter also converts topics to CAN frames that are then transmitted onto the CAN network.

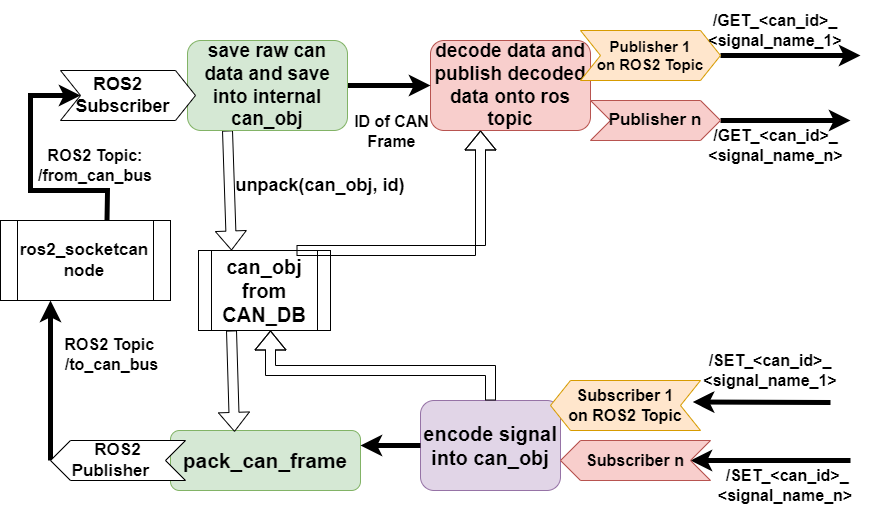
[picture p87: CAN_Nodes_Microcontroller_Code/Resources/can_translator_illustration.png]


### Adding New CAN Frames And Signals
When adding new CAN frames and signals, changes have to be made in the "CAN_DB.dbc" file, new C code has to generated as described in `CAN_Nodes_Microcontroller_Code\CAN_LIBRARY_DATABASE\README.md`. Lastly, the software in hardware interface and low level software has to be adjusted for the newly added frames. This is described in `Hardware_Interface_Low_Level_Computer\HOW_TO_EXTEND.md`.

When adding new CAN frames it is recommended to add new frames and signals instead of changing existing frames/signals. IF EXISTING CAN FRAMES/SIGNALS ARE CHANGED, EXISTING ECUS MUST BE REFLASHED WITH NEW SOFTWARE. If one appends new signals and frames to the database it not strictly necessary to re-flash existing ECUs.

Adding new CAN frames and or signals is described in detail in `CAN_Nodes_Microcontroller_Code\HOW_TO_EXTEND.md`

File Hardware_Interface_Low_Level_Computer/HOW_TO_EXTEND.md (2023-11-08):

## Extend Hardware Interface and Low Level Software
This document aims to describe to process of how to extend the hardware interface and low level software.

Before starting to develop and adding code to the low level control software you need to first make sure you need to add something here. 

If you;

* Want to add a new sensor to autonomous platform
* Want to process sensor information
* Want to design hardware specific interfaces (I.e specific to the electric gokart)

Then you are in the right spot!! 

If not, take a look at `High_Level_Control_Computer` or `CAN_Nodes_Microcontroller_Code`, maybe you intended to add functionality there!

### Prerequisites

In order to start adding functionality it is recommended to have a basic understanding of:

* C++ OR Python development
* docker containers (How to start, stop, restart and configure)
* Linux - The container software environment is mainly navigated in through a terminal
* Robot Operating System 2
* CAN bus

Software wise, you need to have the following installed:

* docker
* git
* VSCode (recommended but any IDE may be suitable)

Hardware wise, it is recommended you have:

* Linux based x86 host computer 

### How to Add New Functionality

First of all make sure you have read the general design principles document for autonomous platform located at `autonomous_platform/HOW_TO_EXTEND.md`. This document takes precedence over anything written in this document in order to unify the development process across all software layers.

This section is split up into two parts;
* [Software Functionality]()
* [Sensors]()
    * [USB Based Sensors]()
    * [Embedded Microcontroller Sensors]()

### Software functionality
If the sensor information already exists and you need to add new software functionality the general implementation steps are:

### Sensors
Sensors can be split up into two groups, sensors with a USB interface and sensors that require an embedded (microcontroller) interface. Integration of sensors that require them to be connected to the embedded ECU. How to add these on the ECU level is described in `CAN_Nodes_Microcontroller_Code/HOW_TO_EXTEND.md`. 

### USB Based Sensors
If a sensors with a USB interface is to be added to autonomous platform then this can be done solely in `Hardware_Interface_Low_Level_Computer` without touching the embedded software. The general procedure would be.

1. Mount the sensor hardware on platform
2. Connect USB to AP4 USB hub.
3. Make sure new device is detected
4. Find suitable existing ROS2 package that fits the given sensor. (Hint: Google)
5. Add ROS2 package installation command into dockerfile
6. Manually start the ROS2 package and see if sensor data is outputted as expected (Hint: ros2 run \${package name} \${node name} OR ros2 launch \${package name} \${launch file name}). Look into package document to see what is available.
7. Configure parameters. Some packages require software to start with certain parameters, if so create a new ROS2 package and save the configuration parameters in this.
8. Configure package dependencies in order to access the downloaded package API
9. Create a launch file, in the newly created ROS2 package, add a launch directory and create a launch file to start the required ROS2 nodes for the USB sensor.
10. Add a `documentation_and_research` folder in the ROS2 package. Write down the steps taken and purpose with package. Document what you have done, if it works as expected etc...
11. Call the newly created launch file for the USB sensor in the main launch file for hardware platform `autonomous_platform\Hardware_Interface_Low_Level_Computer\ap4_hwi_code\ap4hwi_ws\src\launch_hwi_software_pkg\launch\launch_hwi_ros_software.launch.py`
12. Restart platform, everything should start as configured and new sensor information should be available on a topic.

### Embedded Microcontroller Sensors
Once these sensors have been implemented in the ECUs as embedded code and transmitted over the CAN bus network then some development needs to be done in the `Hardware_Interface_Low_Level_Computer` code in order to decode the CAN frame and make the sensor information available on a ROS2 topic.

Once raw CAN bus messages are sent over the CAN bus network and received in the hardware interface low level computer the messages needs to be processed. The general procedure for adding new CAN signals can be seen below:

#### Before you begin
Make sure that that the CAN bus message you want to decode is received over the CAN bus from an embedded ECU. On the Raspberry Pi 4b, perform a candump and analyze it. In a new terminal:
```bash
candump can0
```
The expected output would be similar to:
```bash
  can0  7D0   [8]  00 00 00 00 00 00 00 00
  can0  7D0   [8]  00 00 00 00 00 00 00 00
  can0  7D0   [8]  00 00 00 00 00 00 00 00
  can0  7D0   [8]  00 00 00 00 00 00 00 00
  can0  7D0   [8]  00 00 00 00 00 00 00 00
```
How to analyze; The candump is structured as follows. Each row is a separate CAN frame message consisting.

```bash
<can socket id in HEX format> <Frame ID> <length of CAN frame in Bytes> <Value of bytes in HEX>
```
Meaning;

* can0 : On which CAN socket the CAN bus frame was read from
* 7D0 : The Frame ID (specified in the CAN dbc file)
* [8] : Length of CAN frame. 
* 00 00 00 00 00 00 00 00 : The data sent over CAN bus in HEX

If you see your frame ID that you just added in the embedded software you can continue. If not, go back and look into your newly developed embedded software. Make sure the data is sent as expected, either periodically or when a certain event is triggered. It is not trivial to read and understand the raw hex data, hence we need to programmatically decode this in order to use the data later on.

#### General procedure

A unified standard for the CAN Frames sent across the platform makes the flow of information more intuitive, signal names will have the same name in embedded SW as in ROS2 SW. 

When adding a new CAN bus Frame/Message onto AP4 hardware interface there are a few steps to take: 

HE: ???
<!-- 
1. **Edit the CAN database file** (.dbc) located at `CAN_Nodes_Microcontroller_Code\CAN_LIBRARY_DATABASE  
CAN_DB.dbc` can be opened using kvaser software. Write over the existing file. 
[Simple explanation of CAN dbc file.](https://www.autopi.io/blog/the-meaning-of-dbc-file/#:~:text=DBC%20files%20are%20basic%20text,(i.e.%2C%20CAN%20IDs).) Push to gitlab.  
Note: Editing the database with kvaser has only been tested on Windows 10. 

2. **Generate new CAN_DB.c/h files.**
On a linux host computer, pull down the latest CAN_DB.dbc file. 
Follow the procedure in `CAN_Nodes_Microcontroller_Code\CAN_LIBRARY_DATABASE` README file. Run the "create_database_from_dbc_script.sh". in a terminal.  
Expected output: CAN_DB.c/h in /src/ should be overwritten. (one can delete the existing CAN_DB.h / CAN_DB.c and re run the script to verify that it works)  
Push changes to gitlab.  
Note: Frame names / Signal names are generated according to a standard. Keep this in mind when trying to access a specific signal programmatically later on.
...<Frame_ID>_<Signal_name>...

3. **Create embedded software in ECU.**
See step by step documentation in `CAN_Nodes_Microcontroller_Code`
-->
4. **Update CAN HW Signal to ROS2 TOPIC converter** with new signals.  
Meaning, update the code in can_msgs_to_ros2_topic_pkg. Located at:  
`Hardware_Interface_Low_Level_Computer\ap4_hwi_code\ap4hwi_ws\src\can_msgs_to_ros2_topic_pkg\src\can_msgs_translator_interface.cpp`
 
To describe what does software does in short, this package spawns one ROS2 node which listens to / publishes to,  two topics /from_can_bus and /to_can_bus. These two topics come from the ros2_socketcan ROS2 library.

An illustration for the behavior can be seen in the two figures below:

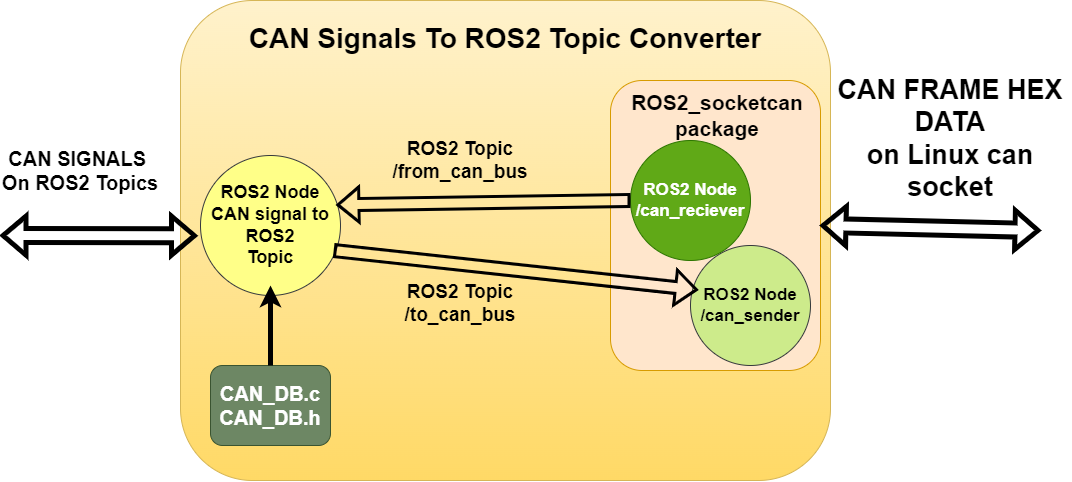
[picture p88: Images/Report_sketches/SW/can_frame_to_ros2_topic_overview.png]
CAN frame to ros2 topic overview
 

 

So therefore, for every CAN signal, there has to be a ROS2 publisher and subscriber.

For every **NEW** CAN signal added in the CAN database file there are five actions which must be taken inside this source file. (can_msgs_translator_interface.cpp) 

NOTE: Signal type is defined in DBC file, choose a suitable type in ROS2. (i.e if Signal in CAN dbc is defined as 8 bit integer, choose Int8 in ROS2). A reference for data type conversion standard between C++ and ROS can be found [here (2.1.1 Fieldtypes)](https://docs.ros.org/en/foxy/Concepts/About-ROS-Interfaces.html).

These ROS2 data types have to be included as message type headers in the top of the file before being able to be used. Example:

```c
#include "std_msgs/msg/string.hpp"
#include "std_msgs/msg/float64.hpp"
#include "std_msgs/msg/int8.hpp"
#include "std_msgs/msg/int16.hpp"
#include "std_msgs/msg/u_int8.hpp"
#include "std_msgs/msg/u_int16.hpp"
...
```

Below:

* \< FRAME ID > should be replaced with the frame ID specified in Kvaser in base 10.
* \<SIGNAL NAME> should be replaced with the signal name outputted into the DBC file from KVASER

The five steps are:

1. Add publisher and subscriber object definitions. (private variables)

Define the class object variables, publisher and subscribers, for EVERY new CAN signal added. Frame ID should be the CAN frame ID set in KVASER, and signal name should be the generated name in CAN_DB file.

```c
// Frame ID XXX publisher
    rclcpp::Publisher<std_msgs::msg::UInt16>::SharedPtr publisher_frame_<FRAME ID>_<SIGNAL NAME>_;

```

```c
// Frame ID XXX subscriber
    rclcpp::Subscription<std_msgs::msg::UInt16>::SharedPtr subscriber_frame_<FRAME ID>_<SIGNAL NAME>_;

```

2. Init publisher and subscriber objects inside class constructor TranslatorCANtoROS2Node()

```c
// Frame ID XXX publisher 
        publisher_frame_<FRAME ID>_<SIGNAL NAME>_ = this->create_publisher<std_msgs::msg::UInt16>("/GET_<FRAME ID>_<SIGNALA NAME>", 10);
```

Each subscriber will have a callback function, when a new ROS2 message is received on a topic and read by the Node, it will call this function to process the message sent over the topic. This definition will come later, as for now, follow the standard and add a callback function according to the naming standard.
```c
// Frame ID XXX subscriber
        subscriber_frame_<FRAME ID>_<SIGNAL NAME> = this->create_subscription<std_msgs::msg::UInt16>("/SET_<FRAME ID>_<SIGNAL NAME>", 10, std::bind(&TranslatorCANtoROS2Node::Callback_frame_<FRAME ID>_<SIGNAL NAME>, this, std::placeholders::_1));

```

3. Add to PublishIncomingDataOnRosTopics()

The switch case should be appended with a new case for every NEW FRAME added. The general idea is to publish every SIGNAL inside a frame onto a unique ROS2 topic, using the publisher objects created above. See the code for inspiration. The structure is the same for every frame. Remember to do this for every SIGNAL in a FRAME.

```c
  switch(frame_id)
        {
            case CAN_ID_REQUEST_HEARTBEAT:
            {
                /*
                publish every can signal contained in frame with id = 100
                */

                /* 
                General procedure for each signal in can frame 
                1: decode data into variable
                2: publish data
            
                */    
                uint64_t temp_data;
                decode_can_0x064_Sig_Req_Heartbeat(&can_storage_container, &temp_data);
                std_msgs::msg::Float64 send_data; 
                send_data.data = temp_data;
                publisher_frame_100_Req_Heartbeat_->publish(send_data);

                break;
            }

            case NEW_FRAME_ID:
            {
                ...
                break;
            }
        }

```

4. Create CALLBACK functions for every ROS2 subscriber.

Example:

```c
// Callbacks for signals in Frame with ID = 1000
    void Callback_frame_1000_Act_BreakVoltage(const std_msgs::msg::UInt16 msg)
    {
        encode_can_0x3e8_Act_BreakVoltage(&can_storage_container, msg.data);
        PublishCanFrameToCanNetwork(CAN_ID_SET_SPCU);
    }
```

```c
// Callbacks for signals in Frame with ID = 1000
    void Callback_<FRAME ID>_<SIGNAL NAME>(const std_msgs::msg::UInt16 msg)
    {
        encode_can_<FRAME ID>_<SIGNAL NAME>(&can_storage_container, msg.data);
        PublishCanFrameToCanNetwork(<FRAME ID>);
    }
```

For every new subscriber created in 1. Create a callback function with the general logic described above.

5. Build the ROS2 Software package.

To check that everything has been setup, try to compile the software. (whilst inside the docker container environment)

* Navigate to ap4hwi_ws directory
* source environment variables
```bash
source /opt/ros/humble/setup.bash
```
Build the ROS2 package
```bash
colcon build
```

Expected output; package built successfully, no errors. 

If nothing else has been changed, push changes to git and pull on the Raspberry Pi 4 on the platform. Restart platform and system should be up and running.

#### How to verify that CAN messages are read and translates properly to a ROS2 topic

Make sure that the platform has the latest code version and that the packages can be built inside the docker container running on the Raspberry Pi 4b.

1. Start up the physical platform
2. Wait for system to boot up
3. Connect display to Raspberry Pi 4b
4. Enter the docker container

```bash
docker exec -it ap4hwi bash
```
Container NOT started? Look in `TEST_DEBUGGING.md` for solutions.

5. Enter correct directory and source environment variables

```bash
cd ap4hwi_ws
source install/setup.bash
ROS_DOMAIN_ID = 1
```

6. Look at what ROS2 topics are available

```bash
ros2 topic list
```

Are there no topics available? Look in `TEST_DEBUGGING.md` for solutions.

In the terminal your newly added ROS2 topic should show up (along with many other topics)

```bash
...
/GET_<FRAME_ID>_<SIGNAL_NAME>
/SET_<FRAME_ID>_<SIGNAL_NAME>
...
```

The information sent over the newly topic can be listen to in the terminal

```bash
ros2 topic echo /GET_<FRAME_ID>_<SIGNAL_NAME>
```

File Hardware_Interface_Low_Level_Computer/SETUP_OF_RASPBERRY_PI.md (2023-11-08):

## Setup Hardware Interface Low Level Code (Raspberry Pi)

This document aims to describe how to configure a fresh Raspberry Pi to run the low level software on the autonomous platform.

In theory this should not have to be done again as the raspberry pi mounted on the platform is already configured. But this document can be useful for future reference if the raspberry pi decides to die.
The end result of following this document should look something like:

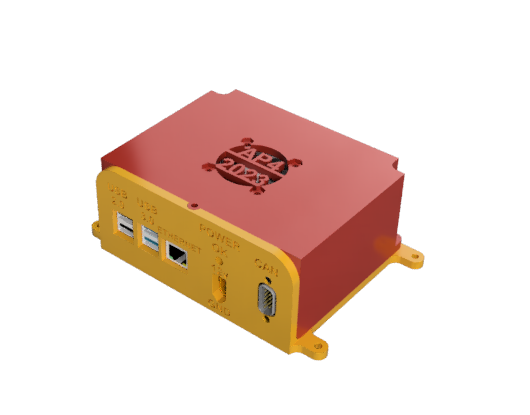
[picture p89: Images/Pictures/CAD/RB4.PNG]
Rendered CAD illustration of outside
 

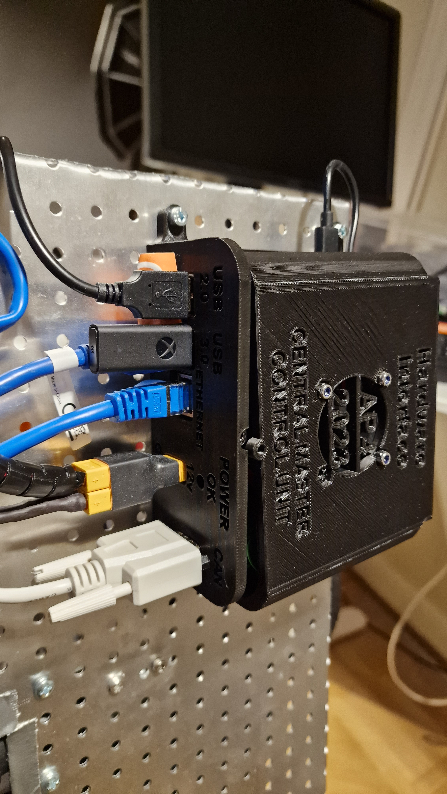
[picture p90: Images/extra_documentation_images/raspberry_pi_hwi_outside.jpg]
Outside view
 

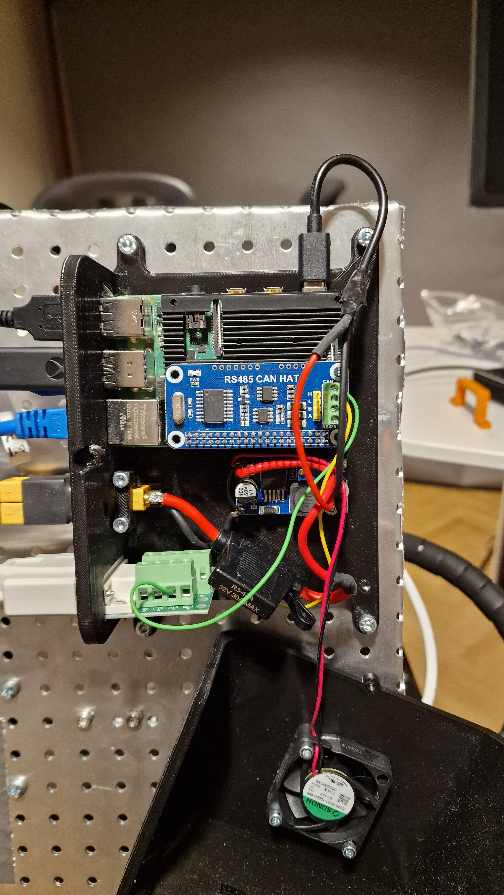
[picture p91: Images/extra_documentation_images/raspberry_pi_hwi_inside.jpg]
Inside view
 

### Required Hardware
This is the required hardware to get the hardware interface low level computer up and running from scratch.

**Components to buy:**

* Raspberry Pi 4b [Link to purchase](https://www.webhallen.com/se/product/358177-Raspberry-Pi-4-Starter-Kit-4-GB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) Recommended 4 or 8 GB RAM version.
* Micro SD card from reputable brand. Minimum recommended size 32GB. 64 is recommended.
* RS485 CAN hat [Link](https://www.amazon.se/CAN-kontroll-SPI-gr%C3%A4nssnitt-s%C3%A4ndtagare-SN65HVD230-l%C3%A5ngdistanskommunikation/dp/B09JKJCMHN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)
* Mini-HDMI to HDMI M-M cable
* LM2596 DC-DC converter
* 40x40x10 12v fan
* XT60 female connector
* DB9 Female connector
* Biltema fuse holder
* 3 A mini fuse
* USB C cable to slice
* M3 nut and bolts
* M4 nut and bolts

**Components to 3D print:**

* Top
* Bottom
* XT60 holder

A computer that can flash a micro sd card is required.

### Installing Base Software on Fresh Raspberry Pi 4b 

- Raspberry Pi 4b, 32 GB micro SD card
- Download Raspberry pi imager v1.7.3 and select Ubuntu 22.04
- Insert micro SD card (recommended minimum size 32gb)
- Connect display cable, mouse, keyboard 
- Plug in power - Raspberry Pi should boot up
- Follow the standard linux installation process presented on screen
- Raspberry pi system configuration
- Name: ap4-hardware-interface
- Computer Name ap4-hw-interface-rpi4
- Username: find it in the main README.md
- Password: find it in the main README.md

Now you can install any new software updates

```bash
sudo apt-get update && sudo apt-get upgrade
```

Restart Raspberry Pi. Can bus hardware setup can be found in 
`autonomous_platform\Documentation\Raspberry_Pi_canbuss_research` directory.

The canbuss communication socket speed can be set using (has to done once every boot-up) (is currently done automatically in startup script)

```bash
sudo apt install can-utils
```

```bash
sudo ip link set can0 up type can bitrate 1000000
```

Docker [installationsguide](https://www.ricmedia.com/tutorials/install-docker-on-raspberry-pi-with-ubuntu)

Install can-utils
```bash
sudo apt-get update && sudo apt-get upgrade
```

### Install GPIO library on raspberry pi running ubuntu

If running a ubuntu distribution on raspberry pi, make sure libraries for controlling the gpio are installed.

```bash
sudo apt install python3-lgpio
```

### Install can-utils library

In order for linux to be able to handle can messages, install can uttils

```bash
sudo apt-get install can-utils
```

### Raspberry pi 4 configuration

There are some software configurations to do in order to enable a can interface using the mcp2515 board. Once configured, the can0 should show up as an available interface when using the command 'ifconfig'

Here is a guide we follow in order to do so: https://www.youtube.com/watch?v=fXiOIUZtV10 and here is a different guide in written format https://harrisonsand.com/posts/can-on-the-raspberry-pi/ 

The MCP2515 module we have is has a clock of 8 Mhz. This is important because it may vary depending on supplier. (The clock frequency should be printed on the clock module on the mcp2515.)

Here is the procedure as described more in detail in the above resources:

1. Update the system
```bash
sudo apt-get update
sudo apt-get upgrade
```

2. Enable SPI bus and load kernel modules:

Using nano editor 

With a raspberry pi 4 running on ubuntu 22.04 this file was located at /boot/firmware/config.txt

hence the command becomes

```bash
sudo nano /boot/firmware/config.txt
```

In this file, append, where 12000000 is the clock frequency of the RS485 hat

```bash
dtparam=spi=on
dtoverlay=mcp2515-can0,oscillator=12000000,interrupt=25 
dtoverlay=spi-bcm2835-overlay
```

3. Reboot raspberry pi

If everything is setup as it should, running the following command should not throw an error

```bash
ifconfig can0
```

### Setting the CAN speed

The canbuss communication speed can be set using

```bash
sudo ip link set can0 up type can bitrate 125000
```
Where 125000 is the speed of the connected canbuss

### Fixing problems with GPIO pins on raspberry Pi

The MCP2515 CAN controller and the TJCxxx tranciever can operate at different voltages. (But are mounted on the same board refered to as MCP2515)

Raspberry Pi GPIO pins are ONLY 3.3V tolerant, meaning the MCP2515 board had to be modified in order for the logic signals from the card to be understood by the raspberry pi. The CAN tranciever MUST be powered from 5V since the CAN is a 5V network.

### Setting up automatic start of software upon boot-up
It is very useful for the software running on the raspberry pi 4b to start when booting up.

This can be done using linux services. The service will call a bash script "testing.bash" located in this directory.

The full procedure can be read [here](https://www.shubhamdipt.com/blog/how-to-create-a-systemd-service-in-linux/).

The steps are summarized below.

in /etc/systemd/system add a new service file. Name it:
```bash
startup_lowlevel.service
```

 With the following contents:

```bash
[Unit]
Description=description about this service
After=network.target
StartLimitIntervalSec=0

[Service]
Type=oneshot
User=root
WorkingDirectory=/home/ap4/Desktop/GIT/autonomous_platform/Hardware_Interface_Low_Level_Computer
ExecStart=/home/ap4/Desktop/GIT/autonomous_platform/Hardware_Interface_Low_Level_Computer/testing.bash

[Install]
WantedBy=multi-user.target
```

Reload linux service file to include the newly created service. 
```bash
sudo systemctl daemon-reload
```
Start the newly created service
```bash
sudo systemctl start startup_lowlevel.service
```

To enable the service to run on boot, enter
```bash
sudo systemctl enable startup_lowlevel.service
```

The status of the service can be observed using
```bash
sudo systemctl status startup_lowlevel.service
```

After this the bash script will execute upon boot-up. And the docker container will always run on startup.

### Testing and debugging (system level)

Here is a list of things to test and verify

* Does it receive CAN messages?
* Can the docker container be started
* Does the docker container start automatically on boot-up?
* Can raspberry pi 4 be pinged from a computer on the same network?

verify that CAN works expected

## Testing and verifying basic functionality

The Raspberry Pi was set up as a CAN sniffer onto the Infotiv CAN lab kit (CAN Education course - Excersise 2). First the kit was setup to run exercise 2 and send temperature over the can bus. The two nodes could send and eceive. Thereafter the raspberry pi was connected onto the CAN bus.  
Some errors occurred such as:

* Make sure the CAN speed is set up right
* The oscillator frequency is set to 8Mhz (NOT 20!!)
* Common ground over the complete CAN system, (GND was connected from lab kit to rasberry pi)

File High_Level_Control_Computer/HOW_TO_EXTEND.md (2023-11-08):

## Extend High Level Software
This document aims to describe to process of how to extend the high level control software.

Before starting to develop and adding code to the high level control software you need to first make sure you need to add something here. 

If you;

* Want to do something with the digital twin
* Work on high level hardware agnostic autonomous drive algorithms
* Evaluate autonomous drive algorithms
* Are NOT adding new hardware
* Are NOT interfacing with the physical platform

Then you are in the right spot!! 

If not, take a look at `Hardware_Interface_Low_Level_Computer` or `CAN_Nodes_Microcontroller_Code`, maybe you intended to add functionality there!

### Prerequisites

In order to start adding functionality it is recommended to have a basic understanding of:

* C++ OR Python development
* docker containers (How to start, stop, restart and configure)
* Linux - The container software environment is mainly navigated in through a terminal
* Robot Operating System 2 (how to create packages and start new nodes)

Software wise, you need to have the following installed:

* docker
* git
* VSCode (recommended but any IDE may be suitable)

Hardware wise, it is recommended you have:

* Linux based x86 host computer, preferably with dedicated graphics (not a must) 

### Add a New Functionality

First of all make sure you have read the general design principles document for autonomous platform located at `autonomous_platform/HOW_TO_EXTEND.md`. This document takes precedence over anything written in this document in order to unify the development process across all software layers.

Software functionality is created inside ROS2 packages. These can be seen as code libraries that are configured to run and perform a specific task within a ROS2 network.

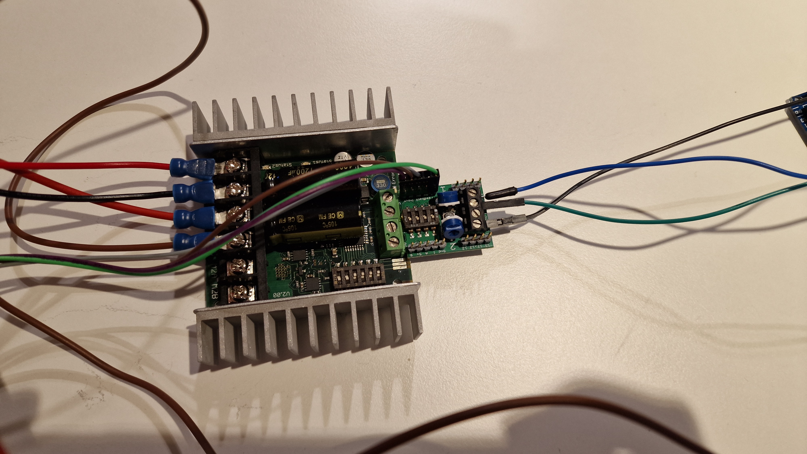
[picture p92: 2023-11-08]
CAN_Nodes_Microcontroller_Code/Shared_HW_Node_Libraries/SteeringMotorInterface/documentation_and_research/images/simplified_serial_wiring2.jpg

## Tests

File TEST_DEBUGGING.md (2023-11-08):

# Testing, Debugging, Known Issues and Future Work

## Test and debugging (System level)

This document collects known problems and issues with the autonomous platform and how to resolve them.

If the existing documentation could not provide a sufficient solution for a problem. Please add your problem and new solution to this document. It will help future members of this project.

### Possible Errors When Starting AP4

Problem: Steering works but not propulsion? 

Solution(s): Check that segway is turned on (and charged), check that the the propulsion can be controlled manually by pressing the pedals. The back wheels should spin.

Problem: Segway is beeping? and wheels are turning backwards

Solution: the segway is in reverse mode, quickly press the brake pedals twice. The beeping should stop and segway should move forward when pressing the accelerator pad.

Problem: Segway is beeping and a yellow/orange light flashes on the front console / nose.

Solution: The batteries for the front black box circuits need to be replaced. Open the black compartment on the nose and replace the 6 AA batteries.

Problem: Neither steering or propulsion works.

Solution: Wait for two minutes, The hardware interface software on the raspberry pi could take a while to boot up

Problem: Neither steering or propulsion works after waiting 2 minutes after power ON.

Solution: Connect a screen (portable small screen) and keyboard + mouse to the raspberry pi to verify that it has booted up properly. 

Sub-problem: Raspberry Pi could not boot up? Or stuck on boot-up sequence?

Solution: Fix errors using command line, try rebooting system. Follow steps down below to make sure the system is working correctly if the raspberry pi has successfully booted up.

1. Check that the Hardware_Interface docker container is running on the Raspberry Pi
In a terminal:

```bash
docker container ps
```
Expected output should look something like this, the important thing is that the container is up and running.

```bash
CONTAINER ID   IMAGE COMMAND CREATED STATUS PORTS NAMES

xxxx   hardware_interface_low_level_computer_ros2   xxxx   10 seconds ago   Up 10 seconds             ap4hwi
```

If the container has not started there are two possibilities: 1. The container is still being built (could take a lot of time if new changes have been pulled). 2. The startup service has not been started properly (could have failed due to docker building errors) [systemd service guide](https://www.shubhamdipt.com/blog/how-to-create-a-systemd-service-in-linux/)

The startup service will run the 'testing.bash' script located in `Hardware_Interface_Low_Level_Computer` once called.

In a terminal check that the service has been started

```bash
sudo systemctl status startup_lowlevel.service
```

output:

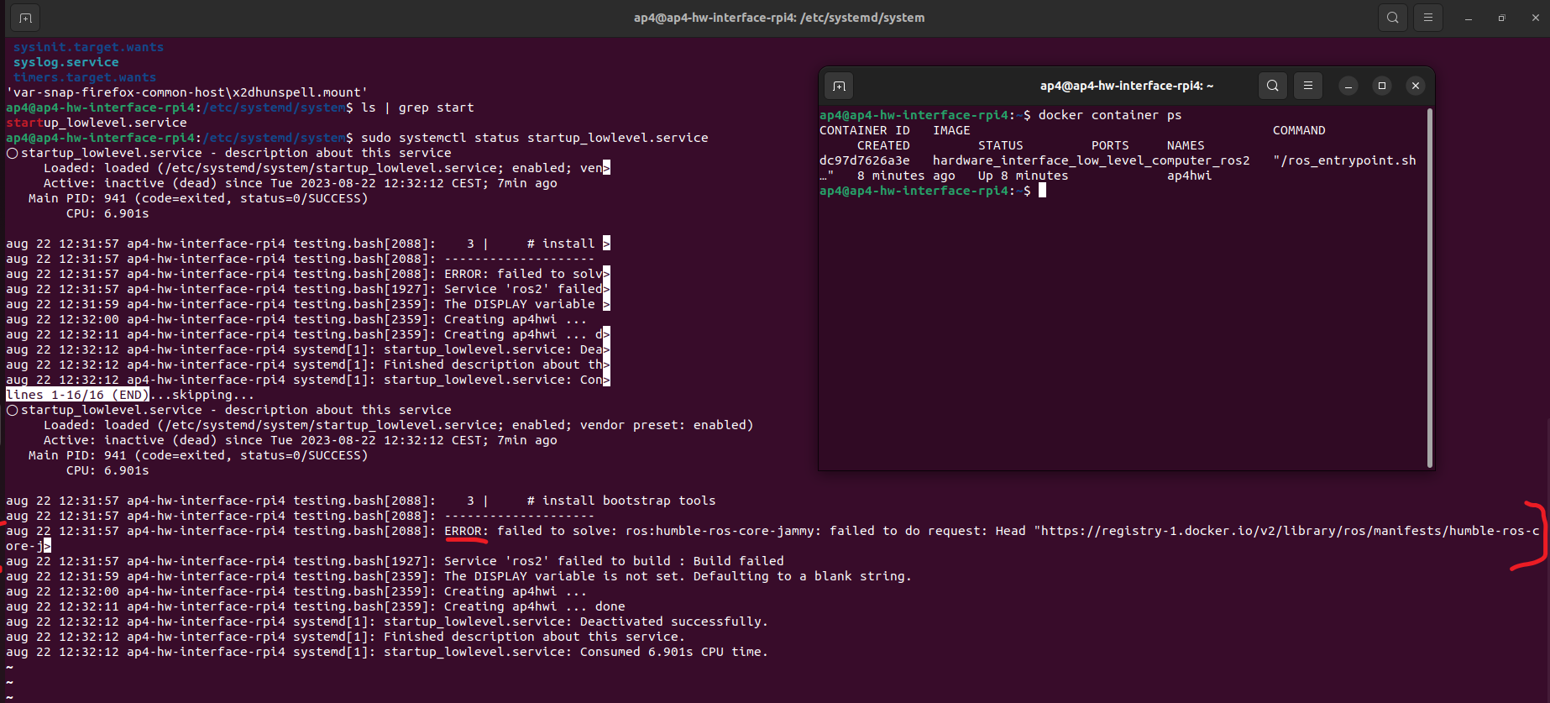
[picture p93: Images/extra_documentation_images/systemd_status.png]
systemd status

In the terminal it would explicity say if something has failed and the service did not start properly. Note that it says ERROR in the screenshot above. Something is therefore wrong! 

### Docker Container starting/Building
If the docker container is not built properly none of the hardware interface software will start properly.

Try rebuilding the docker container:

```bash
cd Desktop
cd GIT
cd autonomous_platform
cd Hardware_Interface_Low_level_Computer
docker-compose build
```

If this fails, there could be something wrong with the dockerfile or docker-compose file.

One possible error is "error creating overlay mount...". See image below.

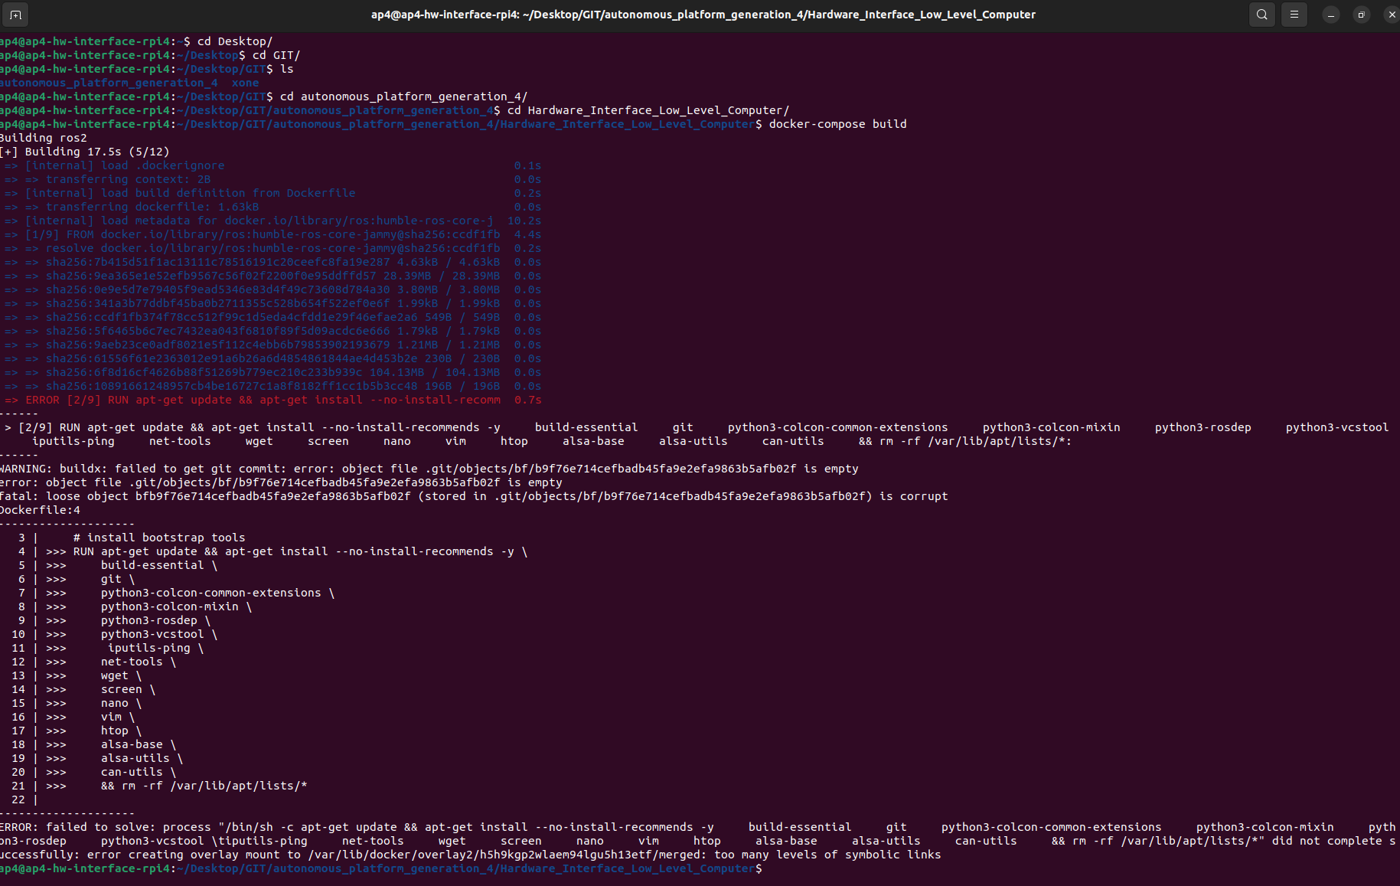
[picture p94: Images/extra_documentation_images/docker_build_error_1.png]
docker build error


This could occur because a specific docker layer could not be built. Try pruning the existing docker caches and rebuilding. (This will take some time on Raspberry Pi hardware, enter the commands and grab some coffee!!) Rebuilding a docker container without any saved caches takes about 10 minutes.

```bash
docker system prune
```

```bash
docker-compose build
```

Another error that has previously occurred can be seen in the image below.

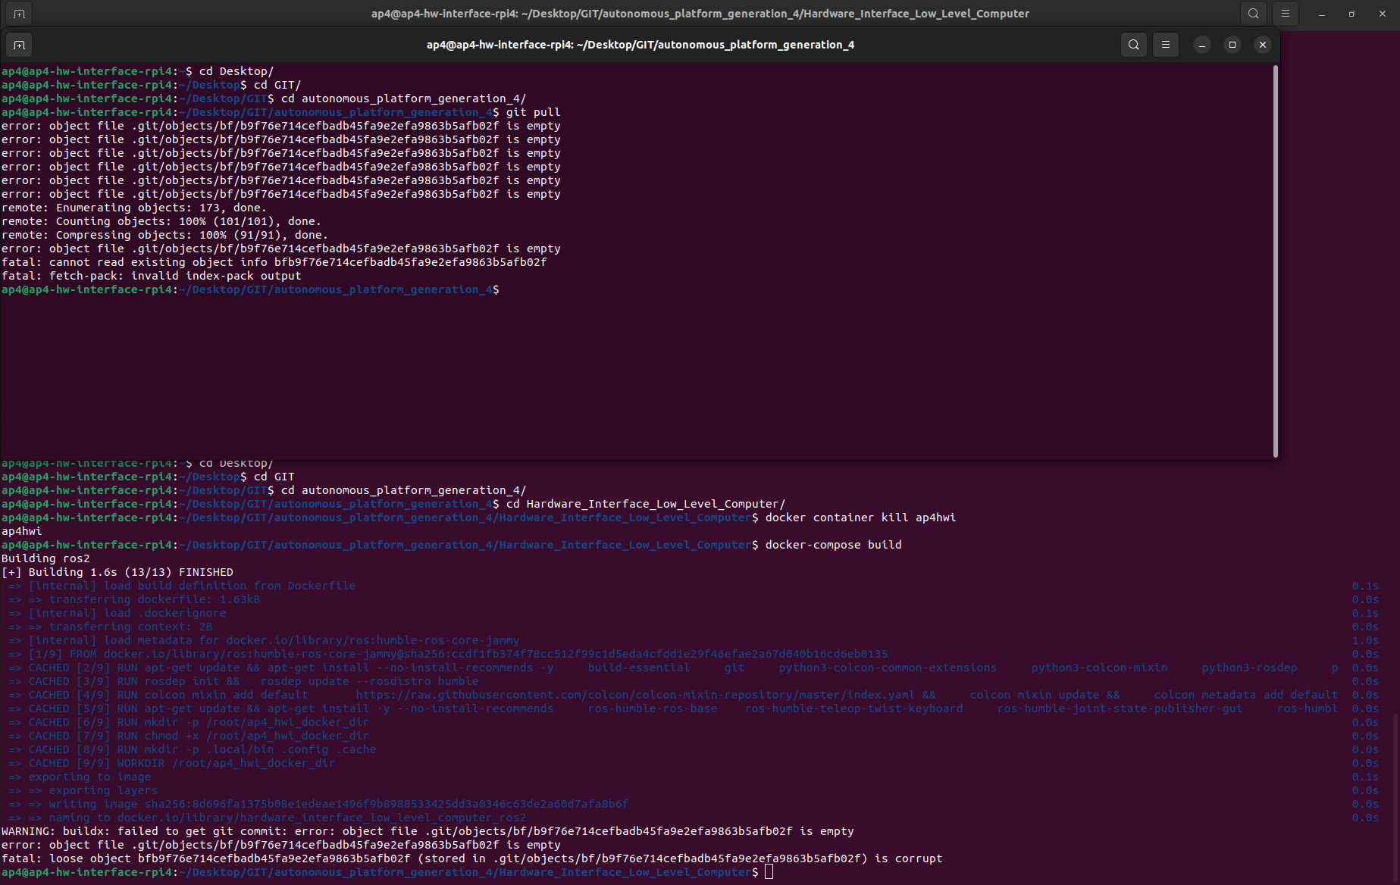
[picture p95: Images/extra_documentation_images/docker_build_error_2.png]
docker_build_error
 Some files in the repository have been corrupted.

To verify that local files are corrupt in the autonomous_platform repository enter the directory and try pulling changes. In a new console:

```bash
cd Desktop
cd GIT
cd autonomous_platform
git pull
```
The output will be something like:

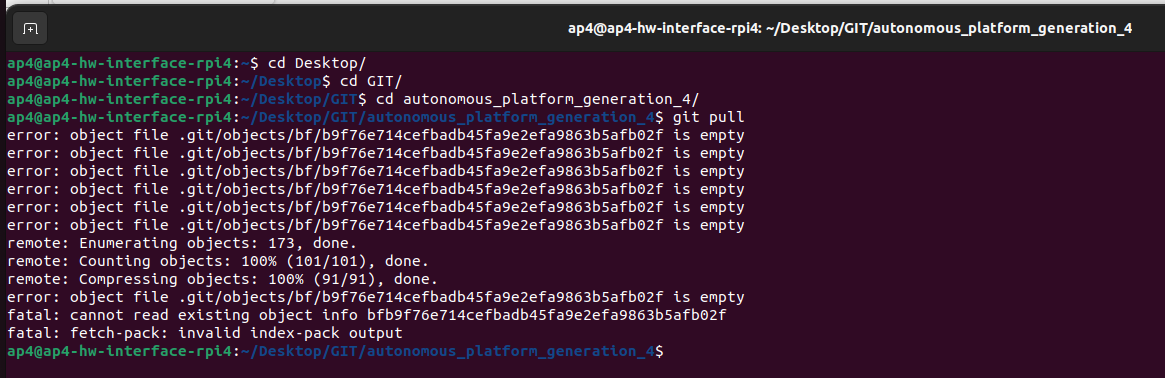
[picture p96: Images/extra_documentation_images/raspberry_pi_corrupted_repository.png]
Raspberry pi corrupted repository


To resolve this issue, delete the corrupted files and pull from gitlab. According to [this](https://stackoverflow.com/questions/4111728/how-do-i-deal-with-corrupted-git-object-files) forum post.

In the repository directory run the following commands:

```bash
find .git/objects/ -size 0 -delete
git pull
```

### Testing and Debugging Components

2. Make sure CAN bus messages are sent and received on linux SocketCAN interface
On the raspberry Pi desktop. Open a new terminal and dump CAN messages
```bash
candump can0
```

Expected output (or similar). The import thing is that can messages are received.

```bash
  can0  7D0   [8]  00 00 00 00 00 00 00 00
  can0  7D0   [8]  00 00 00 00 00 00 00 00
  can0  7D0   [8]  00 00 00 00 00 00 00 00
  can0  7D0   [8]  00 00 00 00 00 00 00 00
  can0  7D0   [8]  00 00 00 00 00 00 00 00
  can0  7D0   [8]  00 00 00 00 00 00 00 00
  can0  5DC   [8]  00 00 00 00 00 00 00 00
  can0  7D0   [8]  00 00 00 00 00 00 00 00
  can0  7D0   [8]  00 00 00 00 00 00 00 00
  can0  7D0   [8]  00 00 00 00 00 00 00 00
  can0  7D0   [8]  00 00 00 00 00 00 00 00
  can0  7D0   [8]  00 00 00 00 00 00 00 00
  can0  7D0   [8]  00 00 00 00 00 00 00 00
  can0  7D0   [8]  00 00 00 00 00 00 00 00
```

If nothing shows up, it means that there is either something wrong with the CAN bus hardware, or in the low-level software.
If the command could not be run, it means that the startup service did not complete and initialize the right commands. (such as sudo ip link set can0 up type can bitrate 1000000) Try rerunning the startup service script by restarting the service.

```bash
sudo systemctl daemon-reload
```

```bash
sudo systemctl enable startup_lowlevel.service
```

The next step is to enter the low level software and rerunning the same command. The output should be the same as above. If this it works it means that the linuxsocketcan has been passed through properly.

```bash
docker exec -it ap4hwi bash
```

```bash
candump can0
```

3. Check that the ROS2 nodes have been launched correctly

First enter the docker hwi container environment
```bash
docker exec -it ap4hwi bash
```

Secondly, enter the correct directory, source environment variables and set the correct environment variables
```bash
cd ap4hwi_ws
source install/setup.bash
export ROS_DOMAIN_ID=1
```

To check which ROS2 nodes are up and running, enter
```bash
ros2 node list
```
The expected output (as of 22/8-2023):

ROS active nodes

If the correct ROS2 nodes have not been started, check that the container built successfully. Try rebuilding the container manually. Make sure the Raspberry Pi has internet access.

IF the container has started properly yet no ROS2 node is up, it can mean that the ROS2 software packages could not be built. To check this, try building them manually and running the ROS2 launch file.

Enter the docker container
```bash
docker exec -it ap4hwi bash
```
Navigate into the ROS2 workspace
```bash
cd ap4hwi_ws
```
Source ROS2 environment
```bash
source /opt/ros/humble/setup.bash
```
Build the low level software ROS2 components
```bash
colcon build
```

It will explicitly output in the terminal how many packages succeeded / failed. A C / Python output will be noted in the terminal. If any of packages failed, resolve the issue wich is presented in the terminal.

Source new ROS2 environment
```bash
source install/setup.bash
```
set environment variable
```bash
EXPORT ROS_DOMAIN_ID=1
```
Run the ROS2 launch file which starts up the software nodes
```bash
ros2 launch launch_hwi_software_pkg launch_hwi_ros_software.launch.py
```

The output should look something similar to this once the startup script has been run:

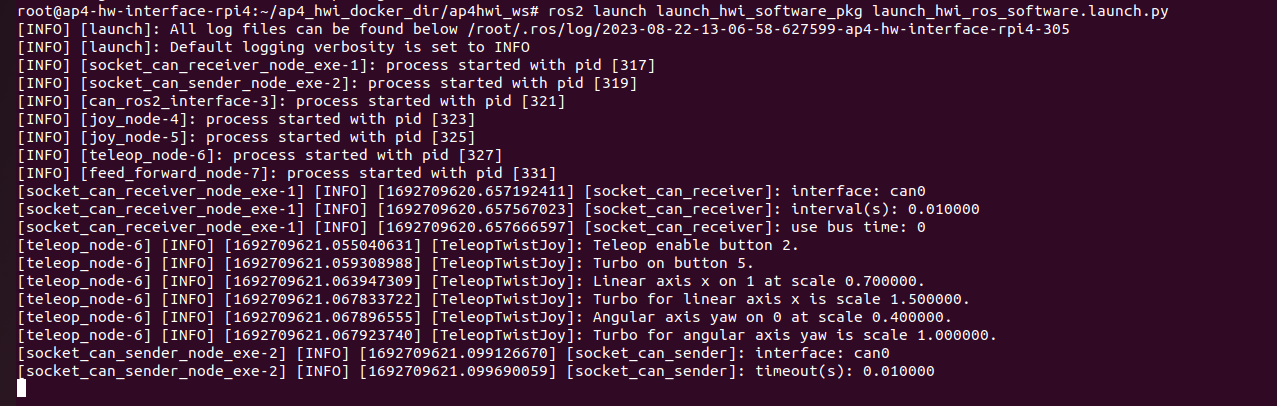
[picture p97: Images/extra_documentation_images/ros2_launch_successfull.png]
ROS2 launch


Try restarting the container and verify that the corrected nodes has been started successfully as described above.

    VERY IMPORTANT: MAKE SURE THAT THE hwi_startup.bash script is actually run when the container is spun up. Look into the docker-compose file in `Hardware_Interface_Low_Level_Computer` directory. 

    There is a command argument. command: xxxxxx

    !!!!!!!!!!!!!!!!!!!!!!
    MAKE SURE THAT #command: /bin/bash -c "./hwi_startup.bash" IS UNCOMMENTED
    !!!!!!!!!!!!!!!!!!!!!!

    Whilst debugging code it can be useful to comment this line out but the software will not start up when the container is started. It will cause a lot of confusion.

This is the expected output when the container is manually started:

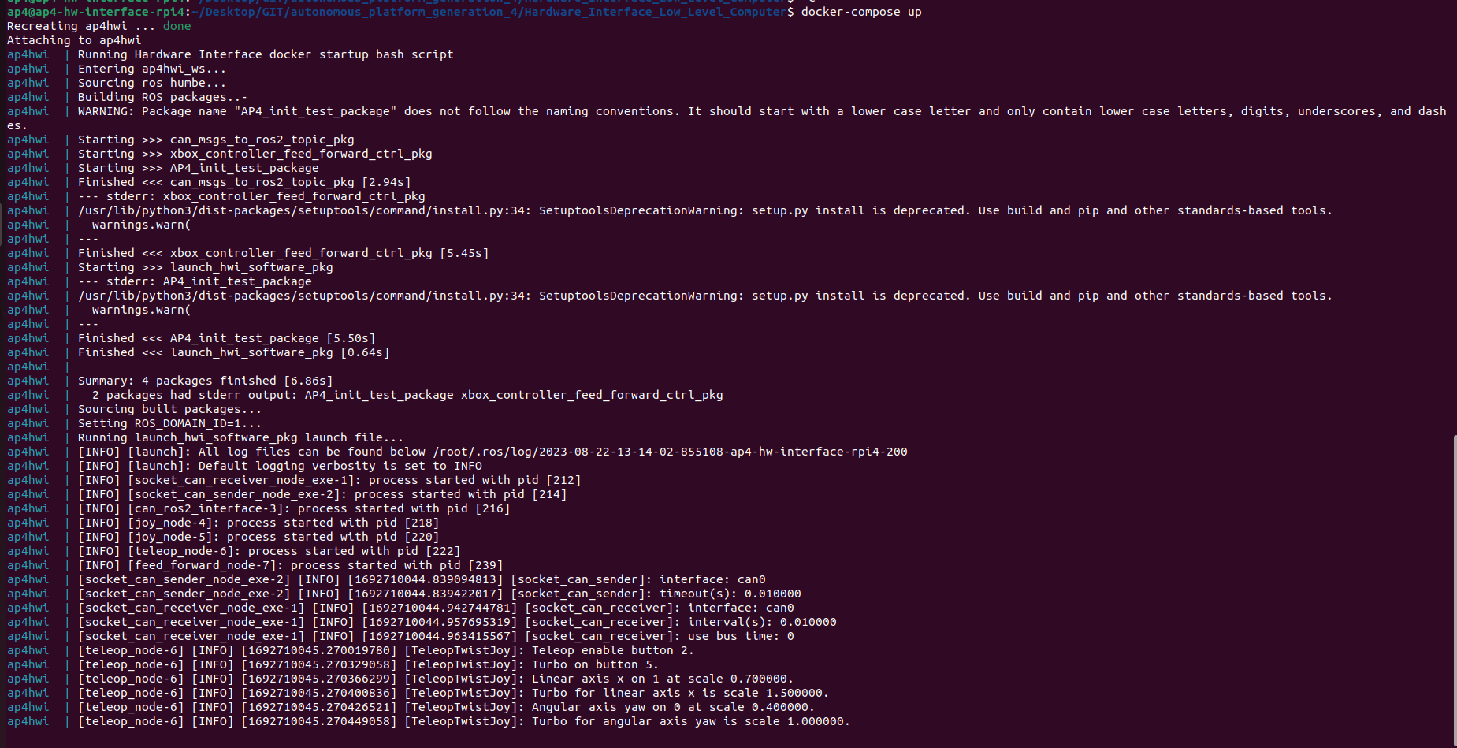
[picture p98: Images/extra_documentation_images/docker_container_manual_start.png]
docker manual start


4. Check communication between low-level-software and SPCU

If the expected ROS2 nodes have been started correctly and the platform still cannot be controlled. Verify that the velocity command from `\cmd_vel` topic is being published on.
```bash
ros2 topic echo /cmd_vel
```

Next, verify that the vehicle controller is outputting desired set voltages for pedals and steering
```bash
ros2 topic echo @TODO ACC + BREAK + STEERING ANGLE
```

Next Verify that the SPCU software and low-level software can communicate. The low-level software can request a ping signal from the ECUs on one topic and receive ping confirmations on another. The ping will be sent over the CAN

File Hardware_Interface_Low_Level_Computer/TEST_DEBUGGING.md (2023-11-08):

## Test and Debugging of Hardware Interface Low Level Computer

This document aims to describe how to test and debugg the low level software if any error occours. If you stumble upon a new error which has been been described below, please add it to the documentation and how you resovled it. It will help future project members.

### Raspberry Pi 4b Bootup failed
The Raspberry Pi 4b can fail to boot-up if there are corrupted files on the micro SD card or if the micro SD card has run out of empty storage. The docker temporary files can grow very large in size.

This is a known issue and is noted down in `ISSUES_AND_FUTURE_WORK.md`.

Connect a display, mouse and keyboard and resolve issues presented in terminal. You probably have to clean something in the filesystem.

If this fails, there is a backup micro SD card containing a copy of the system availible [here](https://infotiv.sharepoint.com/sites/AutonomousPlatform/Delade%20dokument/Forms/AllItems.aspx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) for download. Make sure you have permission to access this project on Infotiv sharepoint. If this does not work, the procedure of setting up a fresh Raspberry Pi 4b is described in `SETUP_OF_RASPBERRY_PI.md` located in this directory.

### Software container not started?
Has the Raspberry Pi 4b booted up without automatically starting the low level software docker container?

There could be several causes for this, some of them are;

* Linux startup service did not run during boot-up
* docker container could not be built due to;
    * Lack of Internet connection
    * Errors in dockerfile configuration 
* Corrupted files on micro SD card.

First, check if the container is running or not using the following command.
```bash
docker container ps
```
If the docker container is running, the expected output would be:
```bash
CONTAINER ID   IMAGE COMMAND CREATED STATUS PORTS NAMES

xxxx   hardware_interface_low_level_computer_ros2   xxxx   10 seconds ago   Up 10 seconds             ap4hwi
```

If the docker container is not running there could be two causes:

* The container is still being built (Can take up to 10 minutes when building from scratch)
* The container failed to build

Either of these alternatives can be verified by looking at the status of the startup service. 
In a terminal check the status of the serive.

```bash
sudo systemctl status startup_lowlevel.service
```

output:

systemd status
In the terminal it would explicity say if something has failed and the service did not start properly. It will also explain exactly what failed. Note that it says ERROR in the screenshot above. Something is therefore wrong! Resolve any issues if present and reboot Raspberry Pi 4b.

### No ROS2 topic shows in terminal
The following command shall display what topics are active on the ROS2 network.
```bash
ros2 topic list
```
The expected output would be similar to:

This section describes how to troubleshoot no topic showing up at all. If some topics show up but not the one you expected, look at `ROS2 Node did not start when starting container` section in this documentation file.

Firstly, make sure you have configured the ROS_DOMAIN_ID environemnt variable
```bash
export ROS_DOMAIN_ID=1
```
If no ROS2 topic still doesn't show up

### ROS2 Node did not start when starting container
First make sure that only a specific node does not start up, if other nodes have started up but not the one you are looking for you need to look in the launch file that starts up the hardware interface software.

Make sure it is configured to automatically start by looking in the launch hwi software package `autonomous_platform\Hardware_Interface_Low_Level_Computer\ap4_hwi_code\ap4hwi_ws\src\launch_hwi_software_pkg\launch`

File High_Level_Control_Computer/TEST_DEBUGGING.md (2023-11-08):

## Testing and Debugging High Level Control Software
This document is meant to document the known errors when running the high level control software and how to solve potential issues that can arise.

If a new unknown error occurs, please write down the solution in this document for future reference.

### Building the high level control software docker container
Build failed? Try to rebuild

### Gazebo and Rviz does not show up when starting the container
Output from console:

    Authorization required, but no authorization protocol specified

Solution: Graphics permission have not been set, the docker container is not allowed to display GUI elements. Run this command from a terminal outside of the container and restart the docker container
```bash
xhost +local:*
```

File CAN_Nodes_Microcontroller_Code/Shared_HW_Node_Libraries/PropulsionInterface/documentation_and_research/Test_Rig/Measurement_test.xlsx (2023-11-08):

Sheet: Demo_test_rig_mount_Ninebot
Time(ms) | Acc | Brake
4194 | 0.73 | 0.75
8388 | 1.96 | 0.75
12582 | 1.96 | 0.75
16777 | 1.96 | 0.75
20971 | 0.73 | 0.75
25165 | 1.96 | 0.75
29360 | 1.96 | 0.75
33554 | 0.73 | 0.75
37748 | 1.96 | 0.74
41943 | 1.96 | 0.75
46137 | 1.96 | 0.75
50331 | 1.96 | 0.75
54525 | 1.96 | 0.75
58720 | 1.97 | 0.75
62914 | 1.96 | 0.75
67108 | 1.96 | 0.75
71303 | 1.96 | 0.75
75497 | 1.96 | 0.75
79691 | 0.73 | 0.75
83886 | 0.73 | 0.75

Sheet: Reverse
Time(ms) | Acc | Brake
0 | 0.76 | 0.79
200 | 0.77 | 0.78
401 | 0.77 | 0.79
602 | 0.77 | 0.78
803 | 0.76 | 0.78
1004 | 0.77 | 0.78
1205 | 0.77 | 2.67
1405 | 0.76 | 1.92
1606 | 0.76 | 2.52
1807 | 0.76 | 2.31
2008 | 0.77 | 0.78
2209 | 0.76 | 0.78
2410 | 0.76 | 0.78
2611 | 0.77 | 0.78
2811 | 0.76 | 0.78
3012 | 0.77 | 0.78
3213 | 0.77 | 0.78
3414 | 0.77 | 0.78
3614 | 0.77 | 0.78
3816 | 0.77 | 0.78
4017 | 0.77 | 0.79
4217 | 0.77 | 0.78
4418 | 0.76 | 0.78
4619 | 0.77 | 0.78
4819 | 0.77 | 0.78
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

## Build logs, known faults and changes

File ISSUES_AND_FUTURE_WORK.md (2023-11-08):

## Known issues

### Priority : Fix known Bugs / Issues 
There are some known bugs and issues and should have priority

* Battery voltage drops during load and steering control is lost
* Lost wifi connection during test day @ gokartcentralen
* Raspberry Pi 4b SD card gets filled with junk files and breaks hardware interface software.

It is a known problem that the raspberry pi 4b fills up with junk files and slows down the raspberry pi and eventually break things. Docker caches also grow in size over time. Possible solution get a bigger SD card? Find how to periodically remove junk files?

* Raspberry Pi 4b corrupted files

Over time files on the SD card gets corrupted and affects behavior.
Common problems are that the docker container cannot be built. A cause for this may be the shutdown procedure of the raspberry pi. Unplugging it to power down may not be optimal. Need to find a solution for properly safely powering down the raspberry pi. Terminal output below.

Raspberry Pi 4b corrupted files

See TEST_DEBUGGING.md to see how it is currently resolved.

* Low voltage input to the raspberry pi makes it slow and unresponsive

Needs to be resolved properly. Could become a problem once more data is sent to and from the hardware interface code.
* PlatformIO build fails when repository is cloned to a path containing a whitespace

Opening the embedded ECU software in platformIO and trying to build it fails when repository filepath has whitespace in it. See error output below. This was when trying to build firmware for SPCU. 

Filepath to SPCU was `C:\Users\erimag\OneDrive - Infotiv AB\Skrivbordet\git\autonomous_platform\CAN_Nodes_Microcontroller_Code\SPCU`

```bash
Linking .pio\build\bluepill_f103c8\firmware.elf
arm-none-eabi-g++: error: Infotiv: No such file or directory
arm-none-eabi-g++: error: AB/Skrivbordet/git/autonomous_platform/CAN_Nodes_Microcontroller_Code/SPCU/.pio/build/bluepill_f103c8/firmware.map: No such file or directory

[.pio\build\bluepill_f103c8\firmware.elf] Error 1
```

I tried the solution presented in this [forum post](https://community.platformio.org/t/spaces-in-path-still-cause-problems-with-g/18214) but could still not get it to work. Temporary solution, clone the repository to a filepath without whitespace?

If there is any error related to long path, open shell as administrator, configure git to use long path names, or else some files will be missed when cloning the repository

```bash
git config --system core.longpaths true
```

## Future work 
As the thesis of 2023 concluded there several functionalities that could not be implemented due to time restrictions. Therefore for future work we suggest:

### Improving Generic ECU nodes with PCB
The generic ECU base hardware should be looked over and iterated over. The I/O proposed should be kept the same to keep compatibility with the rest of the system.

Many loose / Unlabeled Wires coming out from the back of ECU. Hard to follow existing implementation. Cables can be shock loosed by accident very easily.
- Possible solution: Add a 'Phoenix' style connector to the back of the ECU. Standardized connector type and easily available to buy. Would allow for ECU to be easily removed. A specific phoenix connector which fits into the existing size constraints of the ECU needs to be found. Existing CAD model of ECU HW Node needs to be adjusted accordingly. Existing nodes should be upgrades first. Tommy at Infotiv has a product manual with different types of Phoenix Connectors which can be ordered by Infotiv.

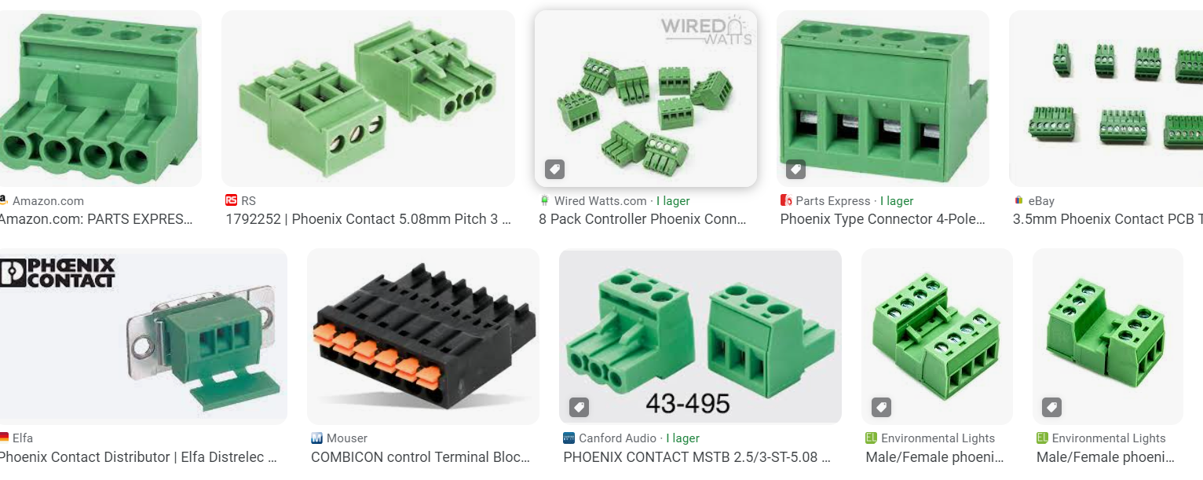
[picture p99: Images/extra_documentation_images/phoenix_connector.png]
Phoenix connector


### Power module
By Power Module it is referring to the battery and Power Supply Unit (PSU).

The power module created during the thesis is sufficient for testing AP4 without anyone sitting in the gokart. During the test day at gokartcentralen (Spring 2023) it was found that the friction of the road surface made the power module insufficient when sitting in the gokart and running from battery power. The power spiked and blew a fuse. On a more slippery surface, such as in the office one could sit in the gokart and drive around without problem.

The voltage from the battery is not regulated, meaning that when the battery depletes the voltage to all the components decreases. Ideally the voltage to the system should remain at a constant 12v.

Current issues with Power Module:

Voltage to the AP4 components drops as battery SoC drops. Could be a cause to unexplained behavior during test day. I.e wifi router stopped working after 3 hours.
- Possible solution: Install a voltage regulator coming out from the battery such that the output voltage from the power module is at a constant 12v regardless of the SoC of battery.

Monitoring power drain during runtime of platform.
- Possible solution: Connect the Voltage sensors and Current Sensor to a ECU and send information to the Central Computer. The hardware for this is installed to battery inside the power module box but has not been connected. By reading voltage and current consumption continuously it could provide useful information to the tests performed and send an alarm when the voltage of the battery gets too low.

Analysis of power consumption of platform is insufficient. Platform blew a fuse unexpectedly whilst sitting in the gokart on a rough surface and turning the steering. The existing analysis (22/8-23) can be found in the thesis report in the 'Images' folder.
- Possible solution: Do a new power requirement analysis of the platform. Taking current spikes into account. Implement changes to the platform to avoid future problems.

### High Level Control Software
The high level control software is very much unfinished. So far a docker container has been setup with the correct environment and software installed.

For future work regarding the digital twin, see __Digital Twin__ section below.

### Digital Twin

The digital twin implemented in spring 2023 is a simple twin created in Gazebo and not very well tuned. The movement dynamics do not behave as the physical AP4 platform does. This needs to be tuned. The dynamics of the physical platform should be investigated, noted down and transferred to the digital twin.

Investigating integration of AP4 into CARLA or other simulations could also be done. As long as the simulation software can integrate with Robot Operating System 2 it should work.

Infotiv already has experience using CARLA for vehicle scenario simulation. Therefore to ease future development of digital twin it could be interesting to transfer the digital twin to the CARLA simulator instead of Gazebo.
- Possible solution:  [ROS bridge installation for ROS2 - Carla Documentation](https://carla.readthedocs.io/projects/ros-bridge/en/latest/ros_installation_ros2/) Note: This is for a previous version of ROS2, AP4 builds on ROS2 Humble so a fix for this needs to be found.

### Mounting High Performance Computer on AP4
During spring 2023, the high performance computer was specified as the development laptop. It was sufficient for testing and connecting wirelessly to the hardware interface (Raspberry Pi 4b). When future AD/ADAS algorithms gets implemented it would be beneficial to have this computing unit mounted permanently onto the platform. This would remove any latency / range issues caused by the platform being controlled over wifi.

Find a suitable Intel NUC mini PC and mount onto the back of Autonomous Platform Generation 4. Install the software currently running on the development laptop onto it.

### Sensor Measurements 
Any Autonomous Drive (AD) or Advanced Driver Assistance System (ADAS) needs sensory input in order to understand its environment and make decision on. As of (22/8-23) the platform does not have such functionality

#### Velocity
A crucial component of any autonomous vehicle is knowing its own state, its velocity is one of such states. During July 2023 Seamus and Alexander started to work on measuring the velocity.

### Camera
A camera sensor can be used to identify obstacles around AP4.

A USB camera (logitech c920) has been bought and mounted to the front of the platform but has not been connected. Some investigation on how to connect is has been done during spring 2023.

The USB hub needs to be connected to the Raspberry Pi 4b (Hardware interface) and onto it the camera needs to be connected. Software wise, a suitable ROS2 camera package should be installed into the low level container. It needs to be configured (through ROS2 launch scripts) to start when the ROS2 software starts up.

Possible suitable ROS2 Camera packages:  https://index.ros.org/r/v4l2_camera/ 

The output from the camera package software would then be a video stream on a known ROS2 topic. This would then need to be processed through some Machine Learning stack to extract useful information (Detected objects, depths, distance, position on road). A ROS2 package would have to be created which listens to the video stream topic and does the computing. Providing the output from the machine learning algorithm on a new ROS2 topic.

### IMU
An Inertial Measurement Unit (IMU) provides information such as linear acceleration and rotation. This information can be useful to determine the orientation and acceleration of the autonomous platform.

This requires an IMU sensor to be integrated onto the platform. See `HOW_TO_EXTEND.md` for general procedure of connecting a new functionality.

### Sensor Fusion
Sensor fusion is the process of combining multiple sensor values in order to get a better approximation of the vehicle state. The information from the sensors above, Camera, Velocity, Lidar and Radar can be combined using sensor fusion algorithms in order to get a better overview of the environment around the autonomous platform.

This can be suitable as a thesis project as it is an advanced topic.

### Testing out existing Autonomous Drive algorithms
When sensors have been integrated onto the platform and sensor data has been processed it can then be used in AD/ADAS algorithms to control the vehicle given its current state.

There exists ready solutions such as OpenPilot. 

Software wise, sensor information on topics needs to be routed to the decision making software. Hamid has great knowledge on how to use OpenPilot.

This was investigated somewhat during the 2023 spring thesis, it was found that OpenPilot ran on Ubuntu 20.04 whilst the software for AP4 runs on ubuntu 22.04. Therefore ROS2 Humble could not be installed in the same container as Openpilot and communication between the decision making software and AP software could not be established.

- Possible solution:
Due to time constraints this could not be investigated further during the masters thesis spring 2023. Possible solutions to the problem presented could be to install ROS2 from source in the OpenPilot docker container, or installing OpenPilot from source in a new docker container running ubuntu 22.04. This has to be investigated further before ruling OpenPilot out as a unsuitable AD software for AP4.

Other alternatives to OpenPilot should be investigated, else it could be interesting to develop an simplified autonomous drive stack in-house at Infotiv.

### Integrating sensors used in the automotive industry
See `HOW_TO_EXTEND.md` on how to integrate sensors which needs to be connected using microcontroller. 

For a list of sensors to possibly integrate see [above](#sensor-measurements) in 'Sensor Measurements'.

Important note added: Once embedded sensors have been implemented according to `HOW_TO_EXTEND.md` information will be available on topic /GET_<FRAME ID>_<SIGNAL_NAME>. This information will then need to be transferred to known standard name topics to make the information flow compatible with the information sent from the digital twin.

I.e velocity commands to the platform should be sent on /cmd_vel {x, y, z, Rx, Ry, Rz} and needs to be converted into commands which can are sent to the platform. I.e "/SET_0x3e8_Act_SteeringPosition", "/SET_0x3e8_Act_ThrottleVoltage" and  "/SET_0x3e8_Act_BreakVoltage". This is performed inside "xbox_controller_feed_forward_ctrl_pkg" (NOTE this package should probably be renamed). Given information on /cmd_vel topic, it is processed and used to control a P-Control, which in turn outputs information on the three topics that are sent to the actuators on the CAN bus.

In a similar way, future sensor information on "/GET_\<FRAME ID>\_\<SIG NAME>" should be processed to output the sensor information on according to naming conventions. This would be done by creating a new package which creates a node. The node would listen to `/GET_\<FRAME ID>\_\<SIG NAME>`, process it (scale, offset, etc) and output the new information on topic `/imu` for example. The output topic should be structured according to how common sensor packages in ROS2 does it, to keep compatibility.

And for velocity specifically, a new ROS2 package should be created, which starts a ROS2 node. It would listen to information on `/SET_0x5dc_Get_Velocity` and output onto `\odom` topic. The output should be on the `\odom` topic using [nav_msgs/msg/Odometry](https://docs.ros2.org/foxy/api/nav_msgs/msg/Odometry.html) type message.

<!-- Note: This should probably be moved to a more appropriate spot in documentation and not future work -->

### Naming of sensor messages convention (sensor interfaces)
[See article link here](https://navigation.ros.org/setup_guides/sensors/setup_sensors.html) under "Sensor Introduction"

There exists a few common packages which specify how sensor messages should be mapped: 

[Full list of ROS2 interfaces can be found here](https://github.com/ros2/common_interfaces)

* [sensor_msgs](https://github.com/ros2/common_interfaces/tree/rolling/sensor_msgs) Examples: Imu, Camera, Joystick, LaserScan, etc
* [radar_msgs](http://wiki.ros.org/radar_msgs)
* [vision_msgs](http://wiki.ros.org/vision_msgs)

### Naming of navigational messages convention (interface)
There exists corresponding interfaces (a given standard) for information sent over the ROS2 network regarding navigation. 

Some navigational interfaces are:

* [nav_msgs](https://github.com/ros2/common_interfaces/tree/rolling/nav_msgs) Example: Odometer interface which represents a current Pose (Position+Orientation) and Velocity
<!-- -->
The goal is to have sensor information from the physical platform have the same data structure and format as the digital twin. And by following a provided standard it allows for easier cross compatibility between created software packages and existing software packages.

See IMU sensor ROS2 topic format [here.](https://subscription.packtpub.com/book/iot-and-hardware/9781783554713/10/ch10lvl2sec100/simulating-imu-on-gazebo)

Sensors which require more data throughput, such as cameras/lidars are often bought as existing solutions and provide USB interface. These can be integrated with AP4 by connecting the sensors to the hardware interface using USB. Software wise there exists ROS2 packages for the commonly used automotive sensors which needs to be installed and configured.

### Automatic and dynamic generation of ROS2 package 'can_msgs_to_ros2_topic_pkg'
This is the ROS2 software package responsible for translating incoming CAN bus data on the Raspberry Pi 4b Hardware_Interface_Low_Level_Computer Linux SocketCAN into useful data on ROS2 topics. Currently it is written by hand and has to be updated every time a new frame or signal is added into the CAN_DB.dbc file for information to flow through the software layers from embedded to low level software. This is a tedious process and can cause a lot of headache if one is not familiar with C++ or the ROS framework.

Future work could therefore be to write a parser (in python?) to automatically generate this package (mainly C++ main.cpp code) using the information stored in the CAN_DB.dbc file.

The current work process is described in `Hardware_Interface_Low_Level_Computer` README file.

One possible issue/problem is how to select what ROS2 common datatype to use. Maybe look into https://docs.ros.org/en/foxy/Concepts/About-ROS-Interfaces.html - Look at Field types. I.e a double in C++ should be defined as a float64 in a ROS2 message.

Autogenerating this code could save a lot of time and headache (Once it has been tested and verified properly). It would also be easier for future AP4 members to add functionality. Messages would only need to be defined in the CAN_DB.dbc file and everything from the embedded structures to the ROS2 interface would be generated automatically.

### Configure docker containers to run on Windows
As of August 2023 the docker containers for autonomous platform are configured to be started on a linux host machine. This is how they are currently configured.

* `High_Level_Control_Computer` container : Starts a graphical simulation of the digital twin. Is meant to run on any linux computer with 3D graphics capability. Is meant to be portable and be started by any member wanting to develop higher level algorithms with the option to run it without being connected to the physical platform.

* `Hardware_Interface_Low_Level_Computer` : Starts the software responsible for interfacing with and controlling the hardware platform. Is meant to be run on a Raspberry Pi 4b connected to the platform.
<!-- -->
To make future development of AD/ADAS algorithms more streamline and more accessible it would be useful to start the high level software container on Windows host machines as well.

A new configuration of the docker-compose file located at `High_Level_Control_Computer` would need to be added. Passing graphical elements out from the container works a bit different on Windows than on a linux host machine. One suggestion would be to use X11 server to display the container desktop GUI inside a web browser. See https://medium.com/geekculture/run-a-gui-software-inside-a-docker-container-dce61771f9 for instructions regarding this option.

### Remote flashing of ECU software over CAN bus
Suggested by Hamid during a meeting, noted down by Erik.

It is quite a bit of a headache to flash the ECUs with new software. If multiple ECUs would have to be re-flashed for some reason it can take quite some time and lead to user errors when moving cables around. When flashing using the ST-Link v3 internal power cables have to be plugged out temporary. This is cumbersome and may lead to user error.

An interesting future work would therefore be to look into flashing the ECUs over the existing CAN bus network remotely.

By flashing over CAN bus, all ECUs can be upgraded automatically when a change have to be pushed. This could in the long term save a lot of time and make the development process pipeline easier to use.

A project with good potential for this functionality can be found [here](https://github.com/crycode-de/mcp-can-boot). It is a software that installs a custom boot-loader onto the embedded microcontroller. This needs to be investigated further to see if it is possible to flash an STM32 bluepill STM32F103C8T6 microcontroller or if can be only be done on other specific hardware.

ECUs on the CAN network could then potentially be flashed by using the sister-repository linked [here](https://github.com/crycode-de/mcp-can-boot-flash-app). This would ideally be run on the Raspberry Pi 4b hardware interface computer

The AP4 CAN bus library used for communication may have to be changed out for the one proposed on the github page mentioned above. 

Here is a list of other similar projects, none specifically for the STM32F103xx though.

* [marcinbor85/can-prog](https://github.com/marcinbor85/can-prog)  - should be looked into
* [Hoernchen20/st-can-flash](https://github.com/Hoernchen20/st-can-flash). 
* [effenco/stm32-can-bootloader](https://github.com/effenco/stm32-can-bootloader)
* [matejx/stm32f1-CAN-bootloader](https://github.com/matejx/stm32f1-CAN-bootloader)
* [Someone successfully implemented STM32103xx bootloader - blogpost](https://stackoverflow.com/questions/61243660/stm32103-custom-bootloader-jump-to-main-firmware-issue)

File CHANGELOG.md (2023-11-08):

### Generation 4 - changelog
Autonomous Platform Generation 4 was started by Fredrik Juthe and Erik Magnusson for their master's thesis during spring 2023. Since then Alexander and Seamus and continued working on it.

AP Generation 4

AP4 was meant as a fresh start for the autonomous platform project, removing the development issues that occurred with AP3 over time. AP4 was designed from the beginning to be a long time project with clear requirements and better development processes.

Another goal with AP4 is to make it more modular then previous versions. Previous versions had many propriety and hardcoded solutions for a specific problems. These could later on affect the development process by making the previous implementations hard to follow.

A new concept which is trialed on AP4 is the concept of "Centralized" Electrical / Electronic (E/E) and software architecture. In short this means that the heavy computations are performed on a centralized computing unit and the ECUs are only responsible for relaying information to and from the computing unit.

It is built on an electric segway gokart platform. Starting from scratch on a new gokart.

###  Version 4, June 2023

AP4 was created by Fredrik Juthe and Erik Magnusson as part of a master thesis at Chalmers University of technology spring 2023. Supervisor: Hamid Ebadi

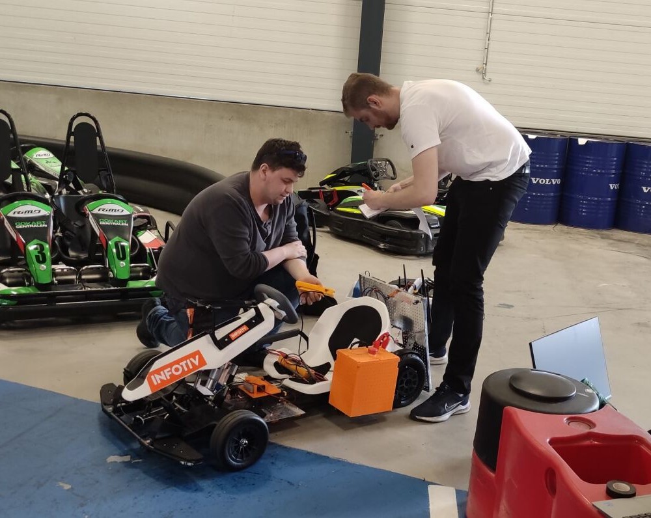
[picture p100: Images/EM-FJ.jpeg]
Fredrik Juthe and Erik Magnusson
 

### Version 4.1, July 2023
Improving documentation and adding speed sensor by 
Seamus Taylor, Alexander Rydevald.  Supervisor: Hamid Ebadi

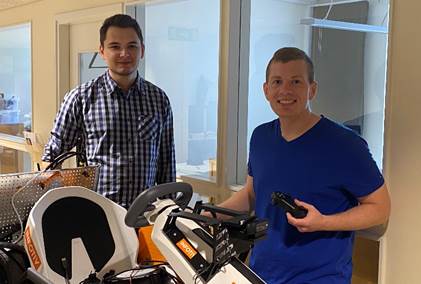
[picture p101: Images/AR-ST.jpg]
Seamus Taylor and Alexander Rydevald
 

### Version 4.1.1 August 2023
Improving documentation, Solving comments left in README files. Refactored repository, removed old/unused files, and made it more clean.
by Erik Magnusson and Seamus Taylor. Supervisor: Hamid Ebadi

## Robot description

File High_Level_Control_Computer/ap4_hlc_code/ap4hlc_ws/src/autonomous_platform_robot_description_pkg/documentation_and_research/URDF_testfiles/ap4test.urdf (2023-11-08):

<robot name="pi_robot">

	<!-- * * * Link Definitions * * * -->

 	<link name="base_link">
		<visual>
		    <origin xyz="0 0 0" rpy="0 0 0"/>
			<geometry>
				<box size="0.9 0.50 0.085"/>
			</geometry>
			<material name="Cyan1">
	       		<color rgba="0 0.9 0.9 1.0"/>
	     	</material>
		</visual>	
	</link>

    <link name="wheel_br_link">
		<visual>
		    <origin xyz="0 0 0" rpy="1.57 0 0"/>
			<geometry>
				<cylinder length="0.1" radius="0.125"/>
			</geometry>
			<material name="temp">
	       		<color rgba="0 0.5 0.1 1.0"/>
	     	</material>
		</visual>	
	</link>

    <link name="wheel_bl_link">
		<visual>
		    <origin xyz="0 0 0" rpy="1.57 0 0"/>
			<geometry>
				<cylinder length="0.1" radius="0.125"/>
			</geometry>
			<material name="temp1">
	       		<color rgba="0.35 0.5 0.1 1.0"/>
	     	</material>
		</visual>	
	</link>
	
    <link name="wheel_swiwel_fl_link">
		<visual>
		    <origin xyz="0.45 0.3 0" rpy="0 0 0"/>
			<geometry>
				<cylinder length="0.1" radius="0.02"/>
			</geometry>
			<material name="temp3">
	       		<color rgba="0.35 0.5 0.4 1.0"/>
	     	</material>
		</visual>	
	</link>

    <link name="wheel_swiwel_fr_link">
		<visual>
		    <origin xyz="0.45 -0.3 0" rpy="0 0 0"/>
			<geometry>
				<cylinder length="0.1" radius="0.02"/>
			</geometry>
			<material name="temp3">
	       		<color rgba="0.35 0.5 0.4 1.0"/>
	     	</material>
		</visual>	
	</link>

    <link name="wheel_fixed_fr_link">
		<visual>
		    <origin xyz="0.45 -0.3 0" rpy="1.57 0 0"/>
			<geometry>
				<cylinder length="0.1" radius="0.02"/>
			</geometry>
			<material name="temp3">
	       		<color rgba="0.35 0.5 0.4 1.0"/>
	     	</material>
		</visual>	
	</link>
	
    <link name="wheel_fl_link">
		<visual>
		    <origin xyz="0 0 0" rpy="0 0 0"/>
			<geometry>
				<cylinder length="0.06" radius="0.075"/>
			</geometry>
			<material name="temp4343">
	       		<color rgba="0.1 0.566 0.1 1.0"/>
	     	</material>
		</visual>	
	</link>
 	
	
	<!-- * * * Joint Definitions * * * -->
	
	<joint name="wheel_br_joint" type="continous">
    	<parent link="base_link"/>
    	<child link="wheel_br_link"/>
    	<origin xyz="-0.45 0.3 0" rpy="0 0 0"/>
	</joint>

    <joint name="wheel_bl_joint" type="continous">
    	<parent link="base_link"/>
    	<child link="wheel_bl_link"/>
    	<origin xyz="-0.45 -0.3 0" rpy="0 0 0"/>
	</joint>
	
    <joint name="wheel_fl_swiwel_joint" type="continous">
    	<parent link="wheel_swiwel_fr_link"/>
    	<child link="wheel_fixed_fr_link"/>
    	<origin xyz="0 0.65 0" rpy="0 0 0"/>
	</joint>

    <joint name="wheel_fl_rotating_joint" type="continous">
    	<parent link="wheel_fixed_fr_link"/>
    	<child link="wheel_fl_link"/>
    	<origin xyz="0.45 -0.25 0" rpy="1.57 0 0"/>
	</joint>

 
</robot>

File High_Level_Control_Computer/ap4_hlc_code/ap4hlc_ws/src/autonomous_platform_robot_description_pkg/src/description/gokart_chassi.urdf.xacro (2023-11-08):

<?xml version="1.0"?>
<robot xmlns:xacro="http://ros.org/wiki/xacro">

 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
  <xacro:property name="base_width" value="0.4"/>
  <xacro:property name="base_length" value="1.02"/>
  <xacro:property name="base_height" value="0.05"/>

  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
  <xacro:property name="backwheel_radius" value="0.125"/>
  <xacro:property name="backwheel_width" value="0.069"/>
  <xacro:property name="backwheel_ygap" value="0.01"/>
  <xacro:property name="backwheel_zoff" value="-0.02"/>
  <xacro:property name="backwheel_xoff" value="${-(base_length)/2 + (backwheel_radius)}"/>
  
  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
  <xacro:property name="frontwheel_radius" value="0.105"/>
  <xacro:property name="frontwheel_width" value="0.080"/>
  <xacro:property name="frontwheel_ygapp" value="0.1"/>
  <xacro:property name="frontwheel_zoff" value="0.080"/>
  <xacro:property name="frontwheel_xoff" value="${ (base_length)/2 }"/>
  
  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
  <xacro:property name="steering_body_extension_length" value="0.075"/>
  <xacro:property name="steering_body_extension_radius" value="0.015"/>
  <xacro:property name="steering_body_extension_zoff" value="0"/>
  <xacro:property name="steering_swiwel_length" value="0.05"/>
  <xacro:property name="steering_swiwel_radius" value="0.025"/>
  <xacro:property name="steering_swiwel_extension_length" value="0.03"/>
  <xacro:property name="steering_swiwel_extension_radius" value="0.015"/>
  
  <xacro:property name="steering_turn_max_limit" value="${pi/5}"/>
  <xacro:property name="steering_turn_min_limit" value="${-pi/5}"/>
  
  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
  <xacro:property name="gokart_frontwing_width" value="0.8"/>
  <xacro:property name="gokart_frontwing_length" value="0.125"/>
  <xacro:property name="gokart_frontwing_height" value="0.025"/>
  <xacro:property name="gokart_frontwing_body_xoff" value="0.16"/>
  
  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
  <xacro:property name="backwheel_weight" value="4.0"/>
  <xacro:property name="frontwheel_weight" value="1.5"/>
  <xacro:property name="chassi_body_weight" value="50.0"/>
  <xacro:property name="frontwing_weight" value="50.0"/>
  <xacro:property name="front_steering_link_weight" value="0.25"/>

  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
  <xacro:include filename="$(find autonomous_platform_robot_description_pkg)/src/description/inertia_macros.xacro"/> 
  


  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
  <link name="base_link">
    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

    <xacro:inertial_box mass="${chassi_body_weight}" x="${base_length}" y="${base_width}" z="${base_height}">
      <origin xyz="0.0 0.0 0.0" rpy="0.0 0.0 0.0"/>
    </xacro:inertial_box>

    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
  </link>
  
    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
  <link name="base_footprint"/>

  <joint name="base_joint" type="fixed">
    <parent link="base_link"/>
    <child link="base_footprint"/>
    <origin xyz="0.0 0.0 ${-(backwheel_radius+backwheel_zoff)}" rpy="0 0 0"/>
  </joint>
  
    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
  <xacro:macro name="wheel" params="prefix x_reflect y_reflect">
    <link name="backwheel_${prefix}_link">
      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

      <xacro:inertial_cylinder mass="${backwheel_weight}" length="${backwheel_width}" radius="${backwheel_radius}" >
        <origin xyz="0 0 0" rpy="${pi/2} 0 0"/>
      </xacro:inertial_cylinder>
    </link>

    <joint name="${prefix}_joint" type="continuous">
      <parent link="base_link"/>
      <child link="backwheel_${prefix}_link"/>
      <origin xyz="${x_reflect*backwheel_xoff} ${y_reflect*(base_width/2)+y_reflect*backwheel_ygap + y_reflect*backwheel_width/2} ${-backwheel_zoff}" rpy="0 0 0"/>
      <axis xyz="0 1 0"/>
      <limit effort="0.1" velocity="20"/>
    </joint>

    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

  </xacro:macro>

  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
  <xacro:wheel prefix="drive_wheel_left" x_reflect="1" y_reflect="1" />
  <xacro:wheel prefix="drive_wheel_right" x_reflect="1" y_reflect="-1" />
  
  
  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
  <xacro:macro name="front_steering" params="prefix x_reflect y_reflect">
  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
    <link name="body_extension_${prefix}_link">
      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

      <xacro:inertial_cylinder mass="${front_steering_link_weight}" length="${steering_body_extension_length}" radius="${steering_body_extension_radius}" >
        <origin xyz="0 0 0" rpy="${pi/2} 0 0"/>
      </xacro:inertial_cylinder>

      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

    </link>
    
    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
    <link name="steering_swiwel_${prefix}_link">
      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

      <xacro:inertial_cylinder mass="${front_steering_link_weight}" length="${steering_swiwel_radius}" radius="${steering_swiwel_length}" >
        <origin xyz="0 0 0" rpy="0 0 0"/>
      </xacro:inertial_cylinder>

      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
    </link>
    
    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
    <link name="swiwel_extension_${prefix}_link">
      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

      <xacro:inertial_cylinder mass="${front_steering_link_weight}" length="${steering_swiwel_extension_length}" radius="${steering_swiwel_extension_radius}" >
        <origin xyz="0 0 0" rpy="${pi/2} 0 0"/>
      </xacro:inertial_cylinder>

      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
    </link>
    
    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
    <link name="frontwheel_${prefix}_link">
      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

      <xacro:inertial_cylinder mass="${frontwheel_weight}" length="${frontwheel_width}" radius="${frontwheel_radius}" >
        <origin xyz="0 0 0" rpy="${pi/2} 0 0"/>
      </xacro:inertial_cylinder>

      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     
    </link>
    
    
   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
    <joint name="$body_extension_${prefix}_joint" type="fixed">
      <parent link="base_link"/>
      <child link="body_extension_${prefix}_link"/>
      <origin xyz="${x_reflect*frontwheel_xoff} ${y_reflect*(base_width/2)+y_reflect*(steering_body_extension_length)/2} ${steering_body_extension_zoff}" rpy="0 0 0"/>
      <axis xyz="0 1 0"/>
    </joint>
    
    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
    <joint name="steering_swiwel_${prefix}_joint" type="revolute">
      <parent link="body_extension_${prefix}_link"/>
      <child link="steering_swiwel_${prefix}_link"/>
      <axis xyz="0 0 1" />
      <limit effort="1" lower="${x_reflect*steering_turn_min_limit}" upper="${x_reflect*steering_turn_max_limit}" velocity="1" />
      <origin xyz="0 ${y_reflect*( steering_body_extension_length )/2 + y_reflect*steering_swiwel_radius} 0" rpy="0 0 0"/>
    </joint>
    
    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
<joint name="swiwel_extension_${prefix}_joint" type="fixed">
      <parent link="steering_swiwel_${prefix}_link" />
      <child link="swiwel_extension_${prefix}_link"/>
      <origin xyz="0 ${y_reflect*(steering_swiwel_extension_length)/2 + y_reflect*steering_swiwel_radius} 0" rpy="0 0 0"/>
      <axis xyz="0 1 0"/>
    </joint>
    
    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
<joint name="frontwheel_${prefix}_joint" type="continuous">
      <parent link="swiwel_extension_${prefix}_link" />
      <child link="frontwheel_${prefix}_link"/>
      <origin xyz="0 ${y_reflect*(steering_swiwel_extension_length)/2 + y_reflect*frontwheel_width/2} 0" rpy="0 0 0"/>
      <axis xyz="0 1 0"/>
      <limit effort="0.1" velocity="5"/>
    </joint>
   
   
  </xacro:macro>
  
  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
  <xacro:front_steering prefix="right" x_reflect="1" y_reflect="1" />
  <xacro:front_steering prefix="left" x_reflect="1" y_reflect="-1" />
  
 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
 <link name="gokart_frontwing_link">
      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

      <xacro:inertial_box mass="${frontwing_weight}" x="${gokart_frontwing_length}" y="${gokart_frontwing_width}" z="${gokart_frontwing_height}">
      <origin xyz="0.0 0.0 0.0" rpy="0.0 0.0 0.0"/>
    </xacro:inertial_box>

      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 
    </link>
 
 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
<joint name="frontwing_joint" type="fixed">
      <parent link="base_link"/>
      <child link="gokart_frontwing_link"/>
      <origin xyz="${base_length/2+gokart_frontwing_body_xoff} 0 ${-gokart_frontwing_height}" rpy="0 0 0"/>
      <axis xyz="1 0 0"/>
    </joint>

</robot>

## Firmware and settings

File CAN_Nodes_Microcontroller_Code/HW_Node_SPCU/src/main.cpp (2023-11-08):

/*
Here is a TLDR description of the HW node

HW_NODE name: Steering and Propulsion Control Unit (SPCU)
Hardware: STM32 Bluepill FC103xx

Purpose of this node:
example:
- Control of steering Motor
- Control of propulsion

Sensor Inputs:
- Encoder readings steering angle
- 

Actuator outputs:
- Serial commands for driver module
- Reference Value for Propulsions Digital to Analog Converters
*/

/*
              Changelog:
_____________________________________________
|   NAME    |   DATE    |       Changes Made        |
_________________________________________________________
|  Fredrik |   27/4-23  |   Base Code for AP4             |
|  Erik    |   25/8-23  |   Removed unnessary comments            |

*/


/*
================================================
Include Arduino libraries to use in project

HOW TO INCLUDE NEW LIBRARIES: Add library in platformio.ini file under lib_deps and they will be downloaded automatically during compiling
This can be done manually or through platformio's library manager.
*/
#include <Arduino.h> // Must Be Included since the PlattformIO uses Arduino Framework

/* Include config files */
#include "pin_config.h"
/*
=================================================
Include custom Controller Area Network (CAN) Database for Autonomous Platform Generation 4.
Make sure this platformio project is located in the CAN_Nodes_Microcontroller_Code directory in order for the relative path to work

Module Libraries are located in: SHARED_HW_Node_Libraries
adding paths to each one is done in platformio.ini
*/
#include "AP4_CAN.h"
#include "PropulsionInterface.h"
#include <SteeringMotorInterface.h>


/* Define and initialie global variables */
KangarooControllInterface steering_motor;
DAC_controller_Interface propulsion_controller;
bool set_SW_filter = false;
AP4_CAN can_interface(CAN_CS_PIN, set_SW_filter);

bool Heartbeat_frame_recieved; 
uint64_t heartbeat_val;
uint64_t heartbeat_val_new;

uint16_t ThrottleVoltage;
uint16_t BreakVoltage;

int8_t steer_pos;

uint32_t t; 
uint32_t t_i1;
uint32_t t_i2;
bool interupt_flag = false;

bool recieved_interrupt = false;
/* Include node specific library dependencies */
// From the lib folder within each project
#include <SPCU_CAN_SETUP.h>


// Interuptfunction declaration 
void AP4CANInterrupt();


// ---------------------------- CODE: ------------------------------

/*
Arduino setup function or also called init
*/
void setup() {
  // note that the void loop() does not have scope to read variables declared within the setup()
  
  //Serial is used for debugging purposes, USB-micro connection cable of the STM32 Bluepill
  //if (SerialUSB){
    Serial.begin(9600);
    //uint32_t t = getCurrentMillis();
    bool break_while=true;
    uint32_t t = getCurrentMillis();
    while(!Serial && break_while)
    {
      uint32_t dt=getCurrentMillis()-t;
      if(dt > (u_int32_t)3000)
      {
        break_while=false;
      }
    }
  
  //Serial3 is used for sending commands to the KANGAROO X2 (drive module for steering modtor)
  Serial3.begin(9600);
  while(!Serial3);
  
  if(propulsion_controller.DAC_init(DAC_Vin,DAC_offset,Serial))
  {
    Serial.println("Propulsion Controll sucessfully initialized");
    encode_can_0x3e8_Act_ThrottleVoltage(&can_interface.can_storage_container,DAC_MIN_OUT_VOLTAGE*CAN_Propulsion_Scale_Up);
    decode_can_0x3e8_Act_ThrottleVoltage(&can_interface.can_storage_container,&ThrottleVoltage);
    propulsion_controller.send_voltage("dac_acc",(float)ThrottleVoltage*(float)CAN_Propulsion_Scale_Down);


    encode_can_0x3e8_Act_BreakVoltage(&can_interface.can_storage_container,DAC_MIN_OUT_VOLTAGE*CAN_Propulsion_Scale_Up);
    decode_can_0x3e8_Act_BreakVoltage(&can_interface.can_storage_container,&BreakVoltage);
    propulsion_controller.send_voltage("dac_break",(float)BreakVoltage*(float)CAN_Propulsion_Scale_Down);
  }
  else{
        Serial.println("Propulsion Controll failed!!");
  }

  
  int iteration = 0;
  bool try_steering_init = true;
  // kangarro might encounter synchornisation problem during initialization, thereby try until establish serial communiation
  while(try_steering_init && iteration < 5)
  {
    if(steering_motor.init(Serial3, InputPortNr, InputMotorNr, InputMotorFixedSpeed, InputWaitForResponseTime, Serial)){
      Serial.println("Steering motor successfully initialized!");
      try_steering_init = false;
      steering_motor.GetLastErrorMsg() ="";
    }
    else {
      Serial.println("Steering motor initialization ERROR!");
      Serial.println("Internal error msg=" + steering_motor.GetLastErrorMsg());
    }
    iteration = iteration+1;
    Serial.println("steering try: " + String(iteration) + "\n");
  }

  // WARNING!!! This should only be necessary when there are two nodes in the system. remove later
  Serial.println("waiting 1 minute for raspberry pi to start!!!");
  delay(60000);

  // Set up of CAN buss
  can_interface.InitMCP2515();
  int nr_can_bus_init_attempts = 0;
  int max_attempts = 500;

  while(can_interface.InitMCP2515() == false && nr_can_bus_init_attempts < max_attempts)
  {
    Serial.println("  INIT OF CANBUSS FAILED! Waiting 1 second and retrying");
    nr_can_bus_init_attempts++;
    delay(1000);
  }


  attachInterrupt(digitalPinToInterrupt(CAN_INTERRUPT_PIN), AP4CANInterrupt, LOW);

  Serial.println("Set up of CAN interface complete!");

  /*
  Configure what CAN signals should be sent (by ID) and in what Periodic intervall (ms) 
  //can_interface.AddPeriodicCanSend(CAN_ID_FRAMENAME, 5000); See CAN_DB.h for frame names
  */
  can_interface.AddPeriodicCanSend(CAN_ID_GET_SPCU,100);
  
  /*
  Configure what CAN signals should be read from the CAN bus (by Id), any other message ID will be ignored!!
  */

  //can_interface.AddCANSWFilter(CAN_ID_FRAMENAME);


  pinMode(LED_BUILTIN, OUTPUT); //internal LED will light up!
  Serial.println("Init of ECU is Complete!");
  Serial.println("");
  t = getCurrentMillis();
  // Engage reverse
  propulsion_controller.send_voltage("dac_break",4);  
  delay(100);
  propulsion_controller.send_voltage("dac_break",DAC_MIN_OUT_VOLTAGE);
  delay(200);
  propulsion_controller.send_voltage("dac_break",4);  
  delay(300);
  propulsion_controller.send_voltage("dac_break",DAC_MIN_OUT_VOLTAGE);
  delay(1000);
  // disengage reverse
  propulsion_controller.send_voltage("dac_break",4);  
  delay(100);
  propulsion_controller.send_voltage("dac_break",DAC_MIN_OUT_VOLTAGE);
  delay(100);
  propulsion_controller.send_voltage("dac_break",4);  
  delay(100);
  propulsion_controller.send_voltage("dac_break",DAC_MIN_OUT_VOLTAGE);
}


/*
"WHILE True-loop"
*/
void loop() {
  uint32_t t_time = getCurrentMillis();

  // the loop function runs over and over again forever
  if(interupt_flag){
    //Serial.println("hello");
    interupt_flag=false;
  }
  can_interface.PeriodicCanSend();
  
  if(recieved_interrupt)
  {
    //decode_can_0x064_Sig_Req_Heartbeat(&can_interface.can_storage_container,&heartbeat_val);
  
  // GET CAN MESSAGE
  can_interface.InterruptReadCAN();

  }

  // Check if error has occured!
  String error_steer = steering_motor.GetLastErrorMsg();
  //String error_prop = propulsion_controller.get_last_error();

  if(!error_steer.equals("no error saved")){
    Serial.println("Error in steering");
    encode_can_0x1f4_Steering_Error(&can_interface.can_storage_container,1);
    can_interface.SendSingleCanFrame(CAN_ID_ERROR_SPCU);
  }  
  if(!propulsion_controller.get_error_in_dac())
  {
    encode_can_0x1f4_Propulsion_Error(&can_interface.can_storage_container,1);
    can_interface.SendSingleCanFrame(CAN_ID_ERROR_SPCU);
  }



// Check if Heartbeat requested
  if(Heartbeat_frame_recieved)
  {
    Serial.println("Heartbeat recieved");
    encode_can_0x065_Response_Heartbeat_sig(&can_interface.can_storage_container,uint8_t(1));
    can_interface.SendSingleCanFrame(CAN_ID_RESPONSE_HEARTBEAT_SPCU);
    Heartbeat_frame_recieved =false;
  }

  // Steering Control:
  decode_can_0x3e8_Act_SteeringPosition(&can_interface.can_storage_container,&steer_pos); //gets stored val
  steering_motor.SetMotorAbsolutePosition(int(map(steer_pos,-40,40,steering_motor.GetSavedMotorMinLimit(),steering_motor.GetSavedMotorMaxLimit())));
  encode_can_0x7d0_Get_SteeringAngle(&can_interface.can_storage_container,steer_pos);


  // Propulsion Control
  decode_can_0x3e8_Act_ThrottleVoltage(&can_interface.can_storage_container,&ThrottleVoltage);
  float temp = (float) ThrottleVoltage*(float)CAN_Propulsion_Scale_Down;
  propulsion_controller.send_voltage("dac_acc",temp);

  decode_can_0x3e8_Act_BreakVoltage(&can_interface.can_storage_container,&BreakVoltage);
  float tempb = (float) BreakVoltage*(float)CAN_Propulsion_Scale_Down;
  propulsion_controller.send_voltage("dac_break",tempb);
  
  uint32_t time_print = getCurrentMillis()-t_time;
  Serial.println("Loop time: " + String(time_print));

  
  /* DEMO CODE BELOW
  Dont forget to comment out steering control and propulsion control above!!!
  propulsion_controller.send_voltage("dac_acc",3);
  
  if (getCurrentMillis()-t> (uint32_t) 5000 && getCurrentMillis()-t < (uint32_t) 5500 ){
    steering_motor.SetMotorAbsolutePosition(int(map(30,-40,40,steering_motor.GetSavedMotorMinLimit(),steering_motor.GetSavedMotorMaxLimit())));
  }
  if (getCurrentMillis()-t> (uint32_t) 10000)
  {
    steering_motor.SetMotorAbsolutePosition(int(map(-30,-40,40,steering_motor.GetSavedMotorMinLimit(),steering_motor.GetSavedMotorMaxLimit())));
    t=getCurrentMillis();
    Serial.println(String(t));
  }
  */
} //END OF WHILE

void AP4CANInterrupt() 
{
  recieved_interrupt = true;
  
}

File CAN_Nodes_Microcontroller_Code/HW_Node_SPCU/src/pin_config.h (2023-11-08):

/*
HW Node pinout configuration for STM32 bluepill fc10308
*/


#define LED_OK_PIN 13

// Configuration for CAN buss communication, same for all nodes:
#define CAN_INTERRUPT_PIN PB12
#define CAN_CS_PIN PA8 

/*
CONFIG for Propulsion Control PINS:

// https://www.electronicshub.org/how-to-use-i2c-in-stm32f103c8t6/
// I2C interface pins for STM32 Bluepill */
#define DAC_SDA PB7
#define DAC_SCL PB6
// IS DEFINED IN Propulsion_config in library path for constant defintions

/*
CONFIG definitions for STEERING CONTROL
*/
#define InputPortNr 1   
#define InputMotorNr 1  
#define InputMotorFixedSpeed 150 
#define InputWaitForResponseTime 1000

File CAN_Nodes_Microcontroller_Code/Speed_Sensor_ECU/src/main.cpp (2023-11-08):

/*
              Changelog:
________________________________________________________________________
|        NAME             |   DATE    |         Changes Made           |
  Alexander Rydevald       07-05-2023      1st draft speed sensor ECU
*/

/*
================================================
Include Arduino libraries to use in project

HOW TO INCLUDE NEW LIBRARIES: Add library in platformio.ini file under lib_deps and they will be downloaded automatically during compiling
This can be done manually or through platformio's library manager.
*/
#include <Arduino.h> // Must Be Included since the PlattformIO uses Arduino Framework
#include <math.h>

/* Include config files */
#include "pin_config.h"
/*
=================================================
Include custom Controller Area Network (CAN) Database for Autonomous Platform Generation 4.
Make sure this platformio project is located in the CAN_Nodes_Microcontroller_Code directory in order for the relative path to work
Module Libraries are located in: SHARED_HW_Node_Libraries
adding paths to each one is done in platformio.ini
*/
#include "AP4_CAN.h"
#include "SpeedSensorInterface.h"

/* Define and initialie global variables */
bool set_SW_filter = false;
AP4_CAN can_interface(CAN_CS_PIN, set_SW_filter);
uint32_t t;
bool recieved_interrupt = false;

uint8_t Velocity; //Variable to store readings from speed sensor

const int LM393 = PA0;    // Connect the sensor output to PA0 pin
volatile unsigned int pulseCount = 0;   // Variable to store the pulse count
unsigned long lastTime = 0;   // Variable to store the last time measurement
unsigned int rpm = 0;         // Variable to store the calculated RPM
unsigned int baud_rate = 9600;         // Variable to store the baud rate
const unsigned int pulsesPerRevolution = 2;   // Number of pulses generated by the sensor per revolution
const double wheelRadius = 0.3;  // Radius of the wheel in meters
const double pi = 3.14159; // Definition of pi

bool interupt_flag = false;
/* Include node specific library dependencies */
// From the lib folder within each project

/*
AP4 CAN read interrupt function
// Interuptfunction declaration*/ 
void AP4CANInterrupt();

// ---------------------------- CODE: ------------------------------

void countPulse() {
  pulseCount++;   // Increment pulse count on each rising edge of the sensor output
}

/*
Arduino setup function or also called init
*/
void setup() {
  // note that the void loop() does not have scope to read variables declared within the setup()

  //Serial is used for debugging purposes, USB-micro connection cable of the STM32 Bluepill
  Serial.begin(baud_rate);
  // Set LM393 as an input pin
  pinMode(LM393, INPUT);   
  // Attach interrupt on rising edge of LM393
  attachInterrupt(digitalPinToInterrupt(LM393), countPulse, RISING);
  // Check if a USB micro cable is connected and serial communication can be connected
  // otherwise, moves on
  bool break_while=true;
  uint32_t t = getCurrentMillis();
  while(!Serial && break_while)
  {
    uint32_t dt=getCurrentMillis()-t;
    if(dt > (u_int32_t)3000)
    {
      break_while=false;
    }
  }

  // Set up of CAN buss, will be needed for every ECU:
  can_interface.InitMCP2515();

  // Set up of CAN buss
  can_interface.InitMCP2515();
  int nr_can_bus_init_attempts = 0;
  int max_attempts = 500;
  // Tries 500 times to setup the CAN bus
  while(can_interface.InitMCP2515() == false && nr_can_bus_init_attempts < max_attempts)
  {
    Serial.println("  INIT OF CANBUSS FAILED! Waiting 1 second and retrying");
    nr_can_bus_init_attempts++;
    delay(1000);
  }
  
  // Send speed sensor by ID (CAN_ID_GE_SPEED_SENSOR) once every second (1000ms).
  can_interface.AddPeriodicCanSend(CAN_ID_GET_SPEED_SENSOR,1000);
  
  /*
  Configure what CAN signals should be read from the CAN bus (by Id), any other message ID will be ignored!!
  */
  attachInterrupt(digitalPinToInterrupt(CAN_INTERRUPT_PIN), AP4CANInterrupt, LOW);

  Serial.println("Set up of CAN interface complete!");

  pinMode(LED_BUILTIN, OUTPUT); //internal LED will light up!
  Serial.println("Init of ECU is Complete!");
  Serial.println("");
}

/*
"WHILE True-loop"
*/

void loop() {

  uint32_t t_time = getCurrentMillis();
  
  if(interupt_flag){
    //Serial.println("hello");
    interupt_flag=false;
  }
  can_interface.PeriodicCanSend();
  // the loop function runs over and over again forever
  if(recieved_interrupt)
  {
  // Updates each value in the can_interface object
  can_interface.InterruptReadCAN();
  }

  // Speed Sensor
  if (millis() - lastTime >= 1000) {   // Check if one second has passed
    unsigned int revolutions = pulseCount / pulsesPerRevolution;   // Calculate the number of revolutions
    
    rpm = (revolutions * 60);   // Calculate RPM based on the number of revolutions
    Velocity = (2 * pi * wheelRadius * rpm) / 60; // Convert RPM to velocity in meters per second
    
    pulseCount = 0;   // Reset pulse count for the next second
    lastTime = millis();   // Store the current time for the next comparison

  }

Serial.print("Velocity: ");
Serial.println(Velocity);   // Print the calculated RPM value
encode_can_0x5dc_Get_Velocity(&can_interface.can_storage_container,Velocity);

}

void AP4CANInterrupt() 
{
  // detects intrupt at the INT pin
  recieved_interrupt = true;
}

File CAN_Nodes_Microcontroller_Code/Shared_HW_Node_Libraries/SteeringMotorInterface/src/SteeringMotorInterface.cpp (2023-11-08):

#include "SteeringMotorInterface.h"
#include <Arduino.h>  //gives access to default arduino library functions, i.e millis()

//init func
KangarooControllInterface::KangarooControllInterface(Stream &inputCmdPort, int inputPortNr, int inputMotorNr, int inputMotorFixedSpeed, int inputWaitForResponseTime) {
  command_serial_port = &inputCmdPort;
  port_nr = inputPortNr;
  motor_nr = inputMotorNr;
  motorFixedSpeed = inputMotorFixedSpeed;
  wait_for_response_time = inputWaitForResponseTime;
  last_error = "no error saved";

  PerformKangarooStartupProcedure();
  
}

KangarooControllInterface::KangarooControllInterface(Stream &inputCmdPort, int inputPortNr, int inputMotorNr, int inputMotorFixedSpeed, int inputWaitForResponseTime, Stream &inputDebugPort) {
  command_serial_port = &inputCmdPort;  //&Serial1; works
  port_nr = inputPortNr;
  motor_nr = inputMotorNr;
  motorFixedSpeed = inputMotorFixedSpeed;
  wait_for_response_time = inputWaitForResponseTime;
  debug_serial_port = &inputDebugPort; //&Serial; works  ;
  last_error = "no error saved";


  PerformKangarooStartupProcedure();  
}

KangarooControllInterface::KangarooControllInterface() {
  port_nr = -1;
  motor_nr = -1;
  motorFixedSpeed = -1;
  wait_for_response_time = -1;
  last_error = "object initialized with empty constructor and values have not been set";

  
}

//explicit init func
//init func
bool KangarooControllInterface::init(Stream &inputCmdPort, int inputPortNr, int inputMotorNr, int inputMotorFixedSpeed, int inputWaitForResponseTime) {
  command_serial_port = &inputCmdPort;
  port_nr = inputPortNr;
  motor_nr = inputMotorNr;
  motorFixedSpeed = inputMotorFixedSpeed;
  wait_for_response_time = inputWaitForResponseTime;
  last_error = "no error saved";

  bool finnished_procedure = PerformKangarooStartupProcedure();
  
  //setup was successful and motor encoder positions have been set
  if( finnished_procedure && motor_max_limit > motor_min_limit) {
    return true;
  }
  else {
    return false;
  }
   
}

bool KangarooControllInterface::init(Stream &inputCmdPort, int inputPortNr, int inputMotorNr, int inputMotorFixedSpeed, int inputWaitForResponseTime, Stream &inputDebugPort) {
  command_serial_port = &inputCmdPort;  //&Serial1; works
  port_nr = inputPortNr;
  motor_nr = inputMotorNr;
  motorFixedSpeed = inputMotorFixedSpeed;
  wait_for_response_time = inputWaitForResponseTime;
  debug_serial_port = &inputDebugPort; //&Serial; works  ;
  last_error = "no error saved";


  bool finnished_procedure = PerformKangarooStartupProcedure();
 
   //setup was successful and motor encoder positions have been set
  if( finnished_procedure && motor_max_limit > motor_min_limit) {
    return true;
  }
  else {
    return false;
  }
}

//set functions
bool KangarooControllInterface::SetSerialPort(Stream &inputPort) {
  command_serial_port = &inputPort;
  return true;
}
bool KangarooControllInterface::SetWaitResponseTime(int inputTime) {
  wait_for_response_time = inputTime;
  return true;
}
bool KangarooControllInterface::SetSerialPortNr(int inputSerialPortNr) {
  port_nr = inputSerialPortNr;
  return true;
}
bool KangarooControllInterface::SetMotorNr(int inputMotorNr) {
  motor_nr = inputMotorNr;
  return true;
}
bool KangarooControllInterface::SetMotorFixedMovementSpeed(int inputMotorFixedSpeed) {
  motorFixedSpeed = inputMotorFixedSpeed;
  return true;
}

//get functions
Stream* KangarooControllInterface::GetSerialPort() {
  return command_serial_port;
 
}
int KangarooControllInterface::GetWaitResponseTime() {
  return wait_for_response_time;
}
int KangarooControllInterface::GetSerialPortNr() {
  return port_nr;
}
int KangarooControllInterface::GetMotorNr() {
  return motor_nr;
}
bool KangarooControllInterface::GetMotorFixedMovementSpeed() {
  return motorFixedSpeed;
}

/*
Returns the saved motor max limit
*/
int  KangarooControllInterface::GetSavedMotorMaxLimit() {
  return motor_max_limit;
}
/*
Returns the sasved motor min limit
*/
int  KangarooControllInterface::GetSavedMotorMinLimit() {
  return motor_min_limit;
}
//Read Motor Information Variables

/*
Reads the controller internal motor encoder position and returns it as an integer
*/
int KangarooControllInterface::ReadCurrentMotorEncoderPosition() {
  String cmd = String(motor_nr) + ",getp\r\n";

  String response = SendSimplifiedSerialCommandWaitForResponse(cmd);

  //if something valid has been read
  if (response != "\0")
  {
    //response should look something like 1,pxxx or 1,Pxxx
    int value = response.substring(3, response.length()).toInt();
    return value;
  }

  return -32768; //max val of integer default return value
}
/*
Function to retrieve the internal stored encoder value for maximum limit of motor
*/
int KangarooControllInterface::ReadMotorEncoderMaxLimit() {
  String cmd = String(motor_nr) + ",getmax\r\n";

  String response = SendSimplifiedSerialCommandWaitForResponse(cmd);

  //if something valid has been read
  if (response != "\0")
  {
    //response should look something like 1,pxxx or 1,Pxxx
    int value = response.substring(3, response.length()).toInt();
    return value;
  }

  return -32768; //max val of integer default return value
}
/*
Function to retrieve the internal stored encoder value for minimum limit of motor
*/
int KangarooControllInterface::ReadMotorEncoderMinLimit() {
  String cmd = String(motor_nr) + ",getmin\r\n";

  String response = SendSimplifiedSerialCommandWaitForResponse(cmd);

  //if something valid has been read
  if (response != "\0")
  {
    //response should look something like 1,pxxx or 1,Pxxx
    int value = response.substring(3, response.length()).toInt();
    return value;
  }

  return -32768; //max val of integer default return value
}
bool KangarooControllInterface::HasReachedTargetPosition() {
  String cmd = String(motor_nr) + ",getp\r\n";

  String response = SendSimplifiedSerialCommandWaitForResponse(cmd);

  //if something valid has been read
  if (response != "\0")
  {
    //response should look something like 1,pxxx or 1,Pxxx
    String cmd = response.substring(4,5);
    //A capital P means the motor has reached its goal position
    if(cmd == "P"){
      return true;
    }
    
  }

  return false;
}

/*
Function to retrieve any error messages that the kangaroo has stumbled upon.
It will only give the latest error message.

*/
String KangarooControllInterface::GetLastErrorMsg()  //returns 1 to 6.
{
  return last_error;
}

/*
=================================================================================================================================================
Set Motor Variables and commands
*/


/*
Sets the absolute motor position (not relative)
Example: 1,p50

From Manual:
Position command. The motor will go to the
specified position, in units
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
